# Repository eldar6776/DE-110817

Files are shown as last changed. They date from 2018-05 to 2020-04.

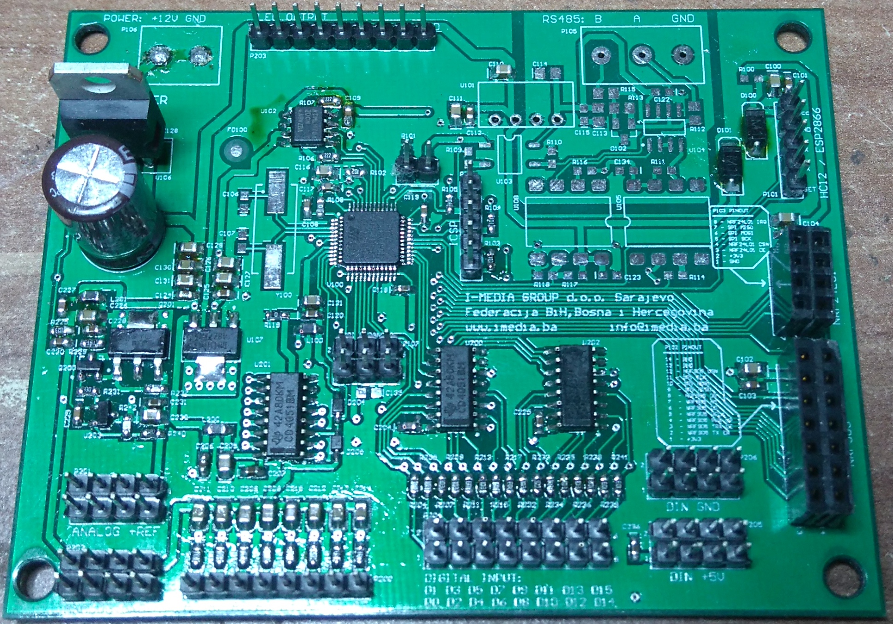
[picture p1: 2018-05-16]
RadioTxImg2.JPG

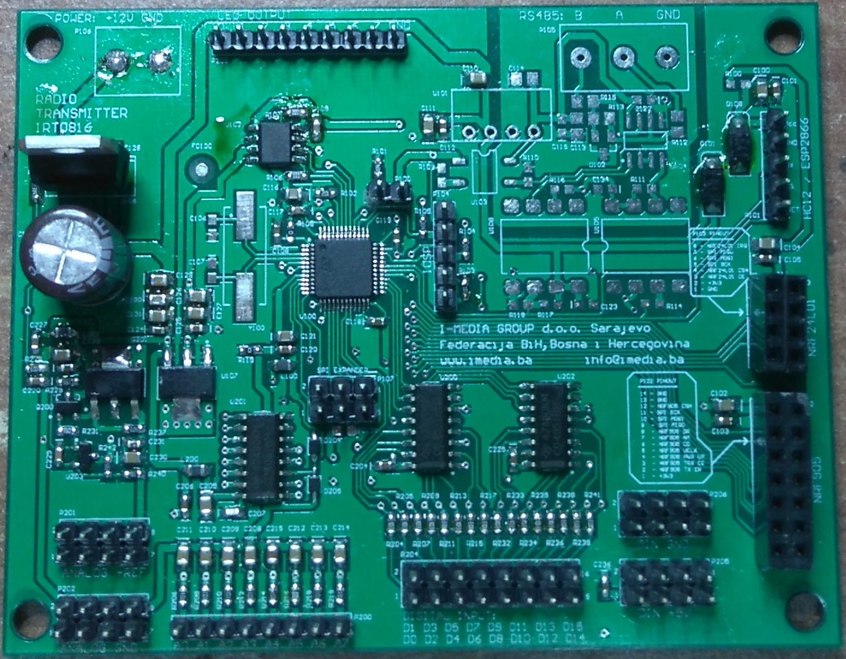
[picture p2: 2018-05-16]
RadioTxImg1.JPG

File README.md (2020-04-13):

# DE-110817
Two-Way Radio Link Transmitter Modul

this is a transmitter for DE-130817 receiver, with a secure radio link to control the concrete pumps. 8 digital inputs are transmitted from the receiver to the transmitter, the PWM driver temperature of 65 degrees Celsius sends a warning to the transmitter, 80 degrees Celsius switches off and blocks the PWM and relay outputs except the oil pump and bypass valve controls. the supply voltage is also monitored. The 433MHz HC-12 radio modules are more than enough range for a stable radio link. if the transmitter does not confirm the transmitter packet longer than 500ms, the receiver switches off the outputs and an LED signal is activated on the transmitter.

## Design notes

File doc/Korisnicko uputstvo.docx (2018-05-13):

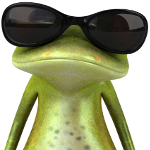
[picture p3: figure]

i MEDIA

__________________________________________________________________________________

Sistem radio kontrole pumpe za beton

Korisničko uputstvo

IRT0816 - Radio predajnik

8 analognih ulaza,

16 digitalnih ulaza,

8 led izlaza.

IRC0816 - Radio prijemnik

8 digitalnih ulaza,

16 relejnih izlaza,

16 PWM izlaza.

Posebne osobine:

- Podesiv indikator napona za većinu baterija ili akumulatora za napajanje predajnika: Nikal-Kadmium, suhi olovni akumulator, Litium-Ion, jednokratne alkalne baterije.
- Predupozorenje prazne baterije ispod 10% kapaciteta.
- Isključenje uređaja kod donjeg nivoa baterije što je ujedno i zaštita akumulatora od dubokog pražnjenja i oštećenja.
- Dvosmjerna radio komunikacija sa sigurnosnom funkcijom isključenja izlaza prijemnika kod prekida komunikacije >500 ms.
- Status prijemnika LED signalima na predajniku + stanje 8 digitalnih ulaza prijemnika koji se mogu koristiti za signalizaciju događaja sa prijemnika npr. min. nivou ulja, pregrijavanju, proradi zaštitnih uređaja, aktiviranju krajnjih ili sigurnosnih prekidača i sl.
- Stabilan izvor pozitivnog napona +3,3Vdc za referentni napon potenciometara spojenih na analogne ulaze.
- Zaštita PWM drivera od pregrijavanja sa signalom predupozorenja.
- RS485 interfejs za žičnu, backup, komunikaciju do 1km sa UTP, FTP, STP kablom za slučaj kvara ili smetnji radio komunikacije.

Fleksibilnost ugradnje:

- Jednostavno uspostavljanje optimalnog radio linka odabirom između 5 različitih radio modula i radnih frekvencija 315MHz, 433MHz, 868MHz, 915MHz, 2,4GHz, plug-and-play izmjenom bez dodatnih podešavanja za sigurnu radio kontrolu.
- Jednostavno podešavanje analognih ulaza za signale sa joystick potenciometara sa nulom na sredini klizača ili za signal potenciometara sa nulom signala na početku klizača
- Podesiva frekvencija PWM drivera za najoptimalniju kontrolu radnog uređaja sa što manjim gubicima i disipacijom temperature izlaznog PWM stepena.
- Mogućnost proširenja analognih/ digitalnih ulaza predajnika kao i pwm/relejnih izlaza prijemnika.
- Mogućnost ugradnje WiFi modula i kontrole prijemnika internet servisima tako da se modul može kristiti u Smart Home sistemu za on/off kontrolu 16~32 potrošača. PWM driver se bez ikakve preinake može koristiti za dimmer kontrolu 5~10 RGB ili 16~32 White LED nizova velike snage. Sa malim izmjenama, t.j. zamjenom tri komponente po kanalu, PWM driver se može transformisat u 16~32 kanalni DAC kojim se generišu kontrolni signali 0~10Vdc, a koji su industrijski standard i ulazni kontrolni signal kod mnogih LED dimmera

Karakteristike periferija:

- Signal na digitalnom ulazu prijemnika ili predajnika < 1Vdc je stanje logičke nule.
- Signal na digitalnom ulazu prijemnika ili predajnika > 2Vdc je stanje logičke jedinice.
- Maximalan pozitivni napon digitalnih ulaza prijemnika ili predajnika je < 30Vdc.
- Maksimalan pozitivni napon analognih ulaza predajnika je < 3,6Vdc.
- Signal na ulazu PWM drivera > 4Vdc postavlja izlaz PWM-a na visoki nivo (napon napajanja PWM drivera).
- Signal na ulazu PWM drivera < 3,5 Vdc postavlja izlaz PWM-a na niski nivo (GND PWM drivera).
- Izlaz PWM-a je N-MOSFET, zbog manjih gubitaka, u high-side switch spoju, t.j. kontrola pozitivnog napona. Upotrebljeni tip je maksimalnog radnog napona 100Vdc i 20A konstantne struje pri temperaturi kućišta do 100°C.
- Za temperature hladnjaka PWM drivera > 65°C aktivira se signal upozorenja na prijemniku.
- Temperatura hladnjaka PWM drivera > 80°C aktivira signal preopterećenja na prijemniku i aktivira zaštitnu funkciju koja isključuje sve izlaze prijemnika i onemogućava aktiviranje dok temperatura hladnjaka ne opadne ispod 65°C.
- Temperaturni senzor temperature hladnjaka PWM-a je NTC otpornik otpora 10K na temperaturi 25°C, na temperaturi 65°C je 2 K, a na temperaturi 80°C je 1,25 K.
- Na svim analognim ulazima su ugrađeni niskopropusni RC filteri ~150Hz koji eliminišu ili uveliko umanjuju smetnje nastale pomjeranjem klizača potenciometara koji su pred kraj radnog vijeka ili su već istrošeni.

Sadržaj uputstva:

1.0 Podešavanje i upotreba modula predajnika ................................... 6
2.0 Podešavanje i upotreba modula prijemnika.................................... 12
3.0 Pregled modula PWM drivera............................................................... 14
4.0 Električne sheme ......................................................................................... 17
5.0 Održavanje uređaja ................................................................................... 19
1. Podešavanje i upotreba modula predajnika :

raspored i namjena konektora na modulu radio predajnika

Kontrolni

taster

Konektor za

signalne LED

Konektor za

RS485 bus

Konektor za

napajanje

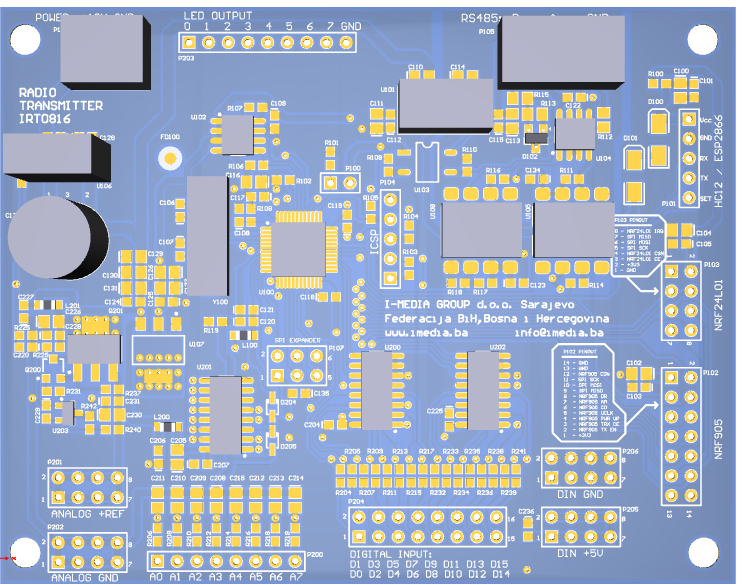
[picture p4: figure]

Konektor za modul proširenja

Konektor za

HC12 radio

modul i WiFi

Konektor za

NRF24L01

radio modul

Konektor za

NRF905 radio

modul

Masa za potenciometre

+3,3Vdc za

potenciometre

Analogni ulazi za potenciometre

Digitalni

ulazi

Masa za digitalne ulaze

+5Vdc za

digitalne ulaze

tabela napona standardnih ćelija

Tip ćelije/ napon | Olovna | Ni-Cd | Ni-MH | Li-ion
Napon ćelije (nominal.) | 2V | 1,2V | 1,2V | 3,7V
Napon pune ćelije | 2,40V | 1,45V | 1,41V | 4,20V
Napon prazne ćelije | 1,75V | 1,00V | 1,00V | 3,20~3,40V

  1.1 Način aktiviranja i izlaz iz funkcije podešavanja

Funkcija za podešavanje modula se aktivira tako da se pritisne kontrolni taster,

a zatim dok je taster pritisnut priključi napajanje predajnika. Sve statusne LED kratkim signalom označavaju da je funkcija aktivna. Nakon što je definisan parametar koji se podešava potrebno je kratko pritisnut kontrolni taster čime se nova vrijednost memoriše u eeprom i odmah je validna. Statusne LED sa tri kratka signala označavaju izlaz iz funkcije za podešavanje.

  1.2 Definisanje analognih ulaza

Kada je digitalni ulaz D0 spojen na +5Vdc i svi ostali digitalni ulazi su slobodni ili spojeni na masu, aktivirana funkcija podešavanja se odnosi na definisanje tipa signala na analognim ulazima. Analogne ulaze na koje će u toku rada uređaja biti spojen signal sa joystick potenciometra treba spojiti na 3,3Vdc, a analogne ulaze koji na koje će biti spojen signal sa standardnog potenciometra treba spojiti na masu. Nakon izlaza iz funkcije podešavanja definisani su analogni ulazi. Veoma je bitno da se ima u vidu da će sve promjene prvom konekcijom biti podešene i na prijemniku. Analogni ulaz predajnika na koji je spojen signal potenciometra joystick-a, na strani prijemnika kontroliše dva PWM izlaza koji su uvijek susjedni, a signal standardnog potenciometra kontroliše jedan PWM. Kada se promjeni definicija analognih ulaza treba i na strani prijemnika utvrditi novi raspored PWM izlaza.

  1.3 Podešavanje napona prazne baterije

Kada je digitalni ulaz D1 predajnika spojen na +5Vdc i svi ostali digitalni ulazi su slobodni ili spojeni na masu, aktivirana funkcija podešavanja se odnosi na definisanje napona prazne baterije. Napon napajanja treba podesiti na napon prazne baterij, a što se može izračunati prema „tabeli napona standardnih ćelija“, tako da se pomnoži broj članaka u bateriji za napajanja sa naponom prazne ćelije za korišteni tip. Najbolje je za napajanje koristiti podesivi izvor istosmjernog napona, a može se koristiti i ispražnjena baterij. Kada je napon definisan, kratko pritisnut kontrolni taster čime je izmjerena vrijednost memorisana kao donji prag napona baterije.

  1.4 Podešavanje napona pune baterije

Kada je digitalni ulaz D2 predajnika spojen na +5Vdc i svi ostali digitalni ulazi su slobodni ili spojeni na masu, aktivirana funkcija se odnosi na podešavanje napona pune baterije. Napon napajanja treba prije podesiti na napon pune baterije, a što se može izračunati prema „tabeli napona standardnih ćelija“, tako da se pomnoži broj članaka u bateriji za napajanja sa naponom pune ćelije za korišteni tip. Najbolje je za napajanje koristiti podesivi izvor istosmjernog napona, a može se koristiti i puna baterija. Kada je napon definisan, potrebno je kratko pritisnut kontrolni taster čime je izmjerena vrijednost memorisana kao napon pune baterije.

  1.5 Podešavanje frekvencije PWM izlaza 0 ~ 15

Kada je digitalni ulaz D3 predajnika spojen na +5Vdc i svi ostali digitalni ulazi su slobodni ili spojeni na masu, aktivirana je funkcija podešavanja frekvencije PWM signala za izlaze od 0 ~ 15. Signalom od 0 do 3,3Vdc na analognom ulazu A0 predajnika se podešava frekvencija PWM izlaza na prijemniku u rasponu od 24Hz do1526Hz. LED signali predstavljaju podešenu vrijednost i to za svaki LED koji svijetli konstantno frkvencija se uvećava za 200Hz, a trepćući signal označava uvećanje za 100Hz. Podešena frekvencija će biti podešena na prijemniku kod prve radio komunikacije sa predajnikom.

  1.6 Podešavanje frekvencije PWM izlaza 16 ~ 31

Kada je digitalni ulaz D4 predajnika spojen na +5Vdc i svi ostali digitalni ulazi su slobodni ili spojeni na masu, aktivirana je funkcija podešavanja frekvencije PWM signala za izlaze od 16 ~ 31. Signalom od 0 do 3,3Vdc na analognom ulazu A0 predajnika se podešava frekvencija PWM izlaza na prijemniku u rasponu od 24Hz do1526Hz. LED signali predstavljaju podešenu vrijednost i to za svaki LED koji svijetli konstantno frkvencija se uvećava za 200Hz, a trepćući signal označava uvećanje za 100Hz. Podešena frekvencija će biti podešena na prijemniku kod prve radio komunikacije sa predajnikom.

  1.7 Provjera statusa baterije

Kratkim pritiskom na kontrolni taster modula predajnika provjerava se status baterije prema LED signalima u rasponu od LED 0 za najmanji nivo do LED 7 za punu bateriju. Nakon 5 sekundi LED signali ponovo označavaju status prijemnika.

  1.8 Provjera statusa radio linka

Kratkim pritiskom na kontrolni taster modula predajnika za vrijeme provjere statusa baterije aktivira se provjera kvaliteta radio linka prema LED signalima u rasponu od LED 0 do LED 7. Ovaj mod ostaje aktivan do novog ciklusa napajanja

ili sledećeg pritiska na kontrolni taster nakon čega se ponovo LED signalima označava status prijemnika. Mjerenjem kvaliteta radio linka se mogu na vrijeme uočiti zone lošeg radio signala i izbjeći zastoji u radu mašine.

  1.9 Nuliranje analognih ulaza

Dužim pritiskom > 3s kontrolnog tastera modula predajnika, kada nije aktivna ni jedna druga funkcija podešavanja ili provjere, te otpuštanjem kontrolnog tastera, signali na analognim ulazima se definišu kao nulte pozicije potenciometara. Prije poziva ove funkcije potrebno je sve potenciometre dovesti u početne ili neutralne pozicije. Za potenciometre joystick-a napon signala u neutralnom položaju je idealno 1,65Vdc, a za ostale potenciometre je napon signala u početnoj poziciji 0Vdc, mada se ovom funkcijom mogu definisati nulte pozicije potenciometara i u bilo kojem drugom položaju npr. kada je signal sa potrošenog potenciometra nestabilan (šušti) na početku hoda, može se nula pomjeriti na dio klizača odakle je signal stabilan. Sve vrijednosti ispod nulte pozicije klizača su jednake nuli signala na izlazu PWM-a.

  1.10 RS485 interfejs za serijsku - backup konekciju

Komunikaciju između predajnika i prijemnika je moguće ostvariti povezivanjem RS485 interfejsa predajnika i prijemnika uvrnutom paricom dužine do 1000 m. Brzina serijske komunikacije je 9600 bps, a format 8-N-1. Ovim interfejsom se korištenjem seta komandi mogu podesiti svi parametri prijemnika i predajnika. Potreban je serijski teminal softver (npr. realterm) i konverter USB/RS485.

  1.11 HC-12 Radio modul

Radna frekvencija je u opsegu 433 – 473MHz podjeljena na 100 kanala. Uz izlaznu snagu od max. 100mW (20dB) i brzinu prenosa do 5000 bps na otvorenom prostoru moguće je ostvariti dvosmjernu komunikaciju do 1000 m. Ako je par ovih radio modula priključen na konektore P3 prijemnika i P101 predajnika, u toku inicijalizacije softvera prvi su odabir za radio link.

  1.12 NRF24L01+PA+LNA Radio modul

Radna frekvencija je 2,4GHz. Izlazna snaga predajnika je >100mW (>20dB), brzina prenosa do 2MB. Na otvorenom prostoru moguće je ostvariti dvosmjernu komunikaciju preko 700 m, brzine prijenosa 1MB. Ako je par ovih radio modula priključen na konektore P5 prijemnika i P103 predajnika, u toku inicijalizacije softvera drugi su odabir za radio link.

  1.13 NRF905 Radio modul

Radne frekvencije su u tri banda 433/868/915MHz. Izlazna snaga predajnika je 10mW (10dB) , brzina prenosa do 50 kbps. Na otvorenom prostoru moguće je ostvariti dvosmjernu komunikaciju do 300 m. Ako je par ovih radio modula priključen na konektore P4 prijemnika i P102 predajnika, u toku inicijalizacije softvera treći su odabir za radio link uspostavljen na bandu 433MHz.

  1.14 LED signalizacija stanja digitalnih ulaza prijemnika i greške

Konektor P203 modula predajnika omogućava monitoring raznih statusa prijemnika i predajnika sa 8 LED dioda koje se spajaju anodama na pinove 1 do 8 konektora P203, a sve katode se spajaju na zajednički pin 9. Serijski otpornici su ugrađeni na modulu i nije ih potrebno dodavati eksterno. Struja izlaza za LED diode sa padom napona od 2V je ~3mA, a za LED diode sa padom napona 3V je ~1mA, što treba uzeti u obzir kada se uređaj napaja baterijama.

Stanje aktivnog digitalnog ulaza na prijemniku se signalizira konstantno svjetlećom LED na predajniku sa istim brojem (LED 0 za digitalni ulaz DIN 0) i obratno, LED je neaktivna kada je digitalni ulaz neaktivan.

Signalizacija greške se označava sa tri kratke promjene stanja LED signala i pauzom od tri sekunde. To znači ako LED svijetli zato što je taj digitalni ulaz aktivan, onda će emitovanje svjetla biti tri puta kratko prekinuto i nakon svake tri sekunde ponovo, a ako je LED bila neaktivna onda će tri puta kratko zasvjetliti i nakon tri sekunde pauze ponavljati ovaj signal.

Značenje signaliziranih grešaka:

LED 0 - napon baterije za napajanje predajnika ispod 10% - upozorenje

LED 1 - baterija za napajanje predajnika prazna - isključenje

LED 2 - greška modula I2C PWM kontrolera - isključenje

LED 3 - temperatura hladnjaka PWM izlaza veća od 65°C - upozorenje

LED 4 - temperatura hladnjaka PWM izlaza veća od 80°C - isključenje

LED 5 - greška NTC temistora za mjerenje temperature PWM - isključenje

LED 6 - prekid radio linka > 500 ms - isključenje

LED 7 - prekid u napajanju prijemnika - isključenje

  1.15 Spajanje analognih ulaza

Svi analogni ulazi su za napone od 0 do 3,3Vdc (!!! NE 5Vdc), za što je na PCB-u modula preajnika obezbjeđen stabilan referentni izvor napona na konektoru P201. Potenciometri na ulazu se spajaju na konektore P200, P201 i P202.

ANALOG +REF (P201)

A0; A1....A7 (P200)

ANALOG GND (P202)

  1.16 Spajanje digitalnih ulaza

Svi digitalni ulazi su predviđeni za ulazni napon do 30Vdc. Na PCB-u modula predajnika se nalaze konektori P204; P205; P206 za dva načina spajanje digitalnih ulaza: sa eksternim izvorom i internim izvorom. Kod spajanja sa internim izvorom, na konektoru P205 je obezbjeđen izvor +5Vdc za beznaponski kontakt koji se drugim izvodom spaja na digitalne ulaze na konektoru P204. Ako se koristi eksterni izvor, minus pol izvora se spaja na DIN GND konektor P206 modula, a pozitivan pol izvora se spaja na digitalne ulaze na konektoru P204. Stanje digitalnog ulaza u odnosu na napon izvora je opisano u dijelu „Karakteristike periferija“.

spajanje digitalnog ulaza za internim izvorom

DIN +5V(P205) D0; D1.....D15 (P204)

spajanje digitalnog ulaza za eksternim izvorom

0~30V D0; D1.....D15 (P204)

GND DIN GND(P206)

  1.17 Spajanje kontrolnog tastera

Za korištenje funkcija: „provjera statusa baterije, provjera statusa radio linka, nuliranje analognih ulaza “, kao i za podešavanja modula predajnika potreban je spoj kontrolnog tastera. Ovaj taster bi trebao biti zaštićen od slučajnog pritiska u toku rada sa predajnikom zbog mogućnosti neželjenog aktiviranja funkcije „nuliranje analognih ulaza“ , a samim tim i zastoja u radu dok se ova funcija ponovo provede.

spajanje kontrolnog tastera

P100/1 P100/2

2. Podešavanje i upotreba modula prijemnika :

raspored i namjena konektora na modulu radio predajnika

LOOP VENTIL

RELEJ 15

RELEJ 9

RELEJ 10

RELEJ 11

RELEJ 12

RELEJ 13

RELEJ 13

RELEJ 14

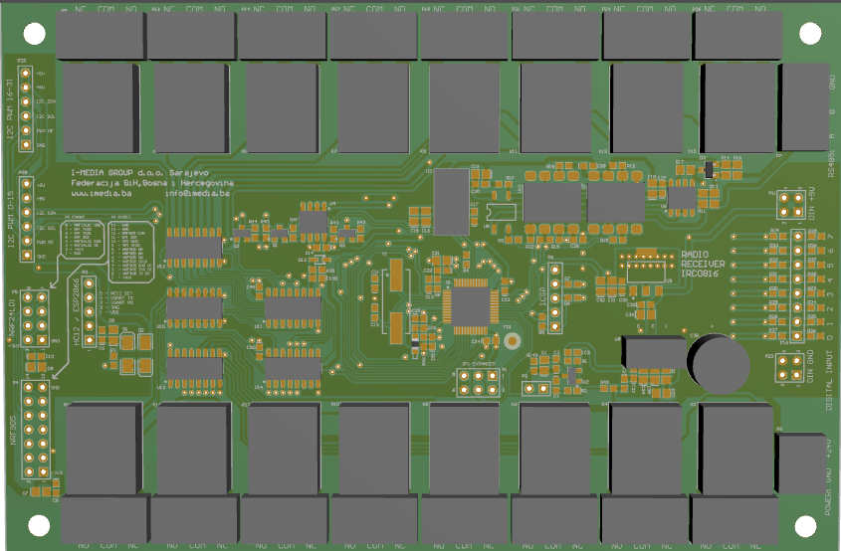
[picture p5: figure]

Konektor NTC senzora

Masa za digitalne ulaze

Konektor za

napajanje

RELEJ 7

RELEJ 6

RELEJ 5

RELEJ 8

RELEJ 4

RELEJ 3

RELEJ 2

RELEJ 1

Konektor za

NRF905

radio modul

Konektor za

PWM kontroler 2

modul

Konektor za

RS485 bus

Digitalni

ulazi

+5Vdc za

digitalne ulaze

Konektor za

NRF24L01

radio modul

Konektor za

PWM kontroler 1

modul

Konektor za

HC12 radio

modul i WiFi

  2.1 NTC senzor temperature hladnjaka PWM izlaza

Tip NTC senzora je pisan u dijelu „Karakteristike periferija“ i korišten je veoma dostupan i najčešće korišteni tip 10K na 25°C. Kada se koristi potrebno je tijelo NTC termistora sa malo termoprovodne paste učvrstiti na hladnjak PWM izlaza i dvožičnim provodnikom spojiti na P2 modula prijemnika. Ovaj provodnik je potrebno odvojiti od provodnika PWM i relejnih izlaza koji su izvor smetnji.

Monitoring teperature hladnjaka PWM drajvera se može isključiti postavljanjem jumpera (kratak spoj) na konektor P2 u slučaju npr. neispravnog NTC termistora ili kada se ne koristi PWM driver.

  2.2 Spajanje digitalnih ulaza

Svi digitalni ulazi su predviđeni za ulazni napon do 30Vdc. Na PCB-u modula prijemnika se nalaze konektori P11; P16; P23 za dva načina spajanje digitalnih ulaza: sa eksternim izvorom i internim izvorom. Kod spajanja sa internim izvorom, na konektoru P11 je obezbjeđen izvor +5Vdc za beznaponski kontakt koji se drugim izvodom spaja na digitalne ulaze na konektoru P16. Ako se koristi eksterni izvor, minus pol izvora se spaja na DIN GND konektor P23 modula, a pozitivan pol izvora se spaja na digitalne ulaze na konektoru P16. Stanje digitalnog ulaza u odnosu na napon izvora je opisano u dijelu „Karakteristike periferija“.

spajanje digitalnog ulaza za internim izvorom

DIN +5V(P11) D0; D1.....D7 (P16)

spajanje digitalnog ulaza za eksternim izvorom

0~30V D0; D1.....D7 (P16)

GND DIN GND(P23)

  2.3 Spajanje PWM kontrolera

Na modul prijemnika je moguće priključiti dva 16 kanalna PWM kontrolera za generisanje PWM signala 0-5Vdc. Kada se koristi drugi PWM kontroler, na prijemniku je potrebno ugraditi modul proširenja analognih ulaza. Rad modula prijemnika je moguć sa i bez modula PWM kontrolera. Ako je modul PWM kontrolera priključen na PCB prijemnika, nakon priključenja napona, softver će registrovati modul i u slučaju kvara ili isključenja u toku rada prijavit će grešku modula te isključiti sve izlaze prijemnika. Ako modul PWM kontrolera nije bio priključen kod uključenja napajanja prijemnika, PWM funkcija izlaza se ne koristi te prijemnik služi kao on/off rejeni kontroler.

Pregled modula PWM drivera :

PCB i raspored komponenti PWM Drivera IPD1624

PWM

izlaz 5

PWM

izlaz 4

PWM

izlaz 3

PWM

izlaz 2

PWM

izlaz 1

PWM

izlaz 0

PWM

izlaz 7

PWM

izlaz 6

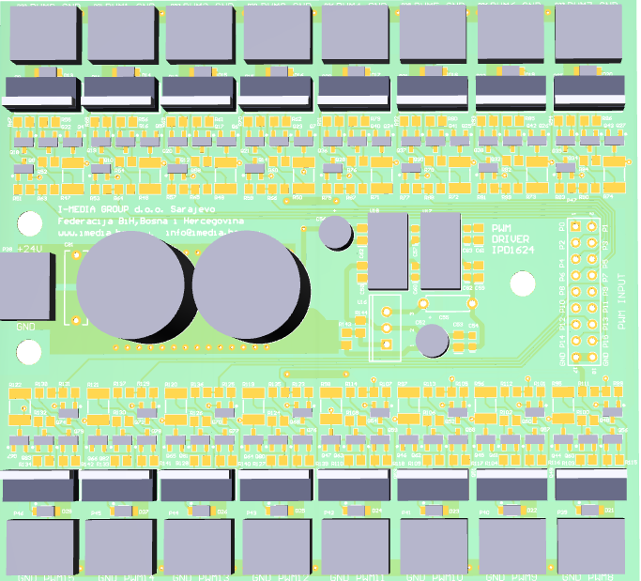
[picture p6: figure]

PWM

izlaz 9

PWM

izlaz 10

PWM

izlaz 11

PWM

izlaz 12

PWM

izlaz 13

PWM

izlaz 14

PWM

izlaz 15

Napajanje

PWM

drivera

PWM

ulazi

0 ~ 15

PWM

izlaz 8

PWM driver IPD1624 je predviđen kao univerzalan PWM izlazni stepen za širok opseg opterećenja i radnih napona, te kao takav nema implementiranu prekostrujnu zaštitu i koju je potrebno izvesti eksterno prema opterećenju koje se spaja na izlaz. Zaštita se može izvesti serijskom vezom staklenog rastalnog osigurača (tromog T ili brzog F) i priključenog opterećenja t.j. radnog uređaja (proporcionalni elektro ventil, servo pozicioner, aktuator), a što treba provjeriti u specifikaciji za taj uređaj. Primjer spoja zaštite je skiciran ispod.

SF52 (5A, 100V)

ventil

T2A

PWM GND

izlaz osigurač

Niti na jedan od PWM izlaza drivera se ne smije priključivati izvor napajanja bilo da je PWM driver priključen na napajanje ili da je napajanje isključeno. Ovo bi za posljedicu imalo pregorijevanje gate otpornika izlaznog MOSFET-a, zaštitne zener diode ili pnp gate-driver tranzistora.

Ukoliko je potreban bilo kakav paralelan rad PWM drivera i nekog drugog kontrolnog sklopa, potrebno je ili napraviti preklopnik ručna komanda – radio komada ili na izlaz PWM-a koji je u paralelnom spoju sa dodatnom kontrolom ugraditi diodu za blokadu pozitivnog napona sa izlaza prema unutrašnjem sklopu PWM drivera. Dioda treba biti dimenzionisana prema struji priključenog opterećenja. Treba voditi računa da je pad napona na diodi oko 0,5 V što uz veću struju opterećenja od npr. 2A daje disipaciju od 1W, tako da je potrebno pobrinuti se za odvođenje viška toplote sa diode na hladnjak .

spoj za preklopnik ručna komanda – radio komada

SF52 (5A, 100V)

PWM

T2A

izlaz

ventil

GND

Ručna

komanda

relej

Odabir

kontrole

spoj za blokadu pozitivnog napona sa ručne kontrole prema PWM driveru

MBRF20100CT SF52 (5A, 100V)

ventil

T2A

PWM

izlaz

GND

Ručna

komanda

Na sva induktivna opterećenja kontrolisana PWM driverom koja nemaju ugrađen snubber, obavezno je ugraditi flyback diodu bar duplo veće struje od struje kontrolisanog induktiviteta i bar duplo većeg reversnog napona od napona napajanja PWM drivera. Bez eliminisanja smetnji koje nastaju kod isključenja napajanja induktivitetu, moguća su spontana, nekontrolisana uključenja izlaza PWM drivera kao i nekontrolisani reseti mikrokontrolera.

spoj flyback - zaštitne diode na induktivno opterećenje (elektroventil 2A, 24Vdc)

SF52 (5A, 100V)

T3,15A

ventil

PWM GND

izlaz

Električne sheme :

spajanje modula PWM kontrolera, PWM izlaza i radio modula prijemnika

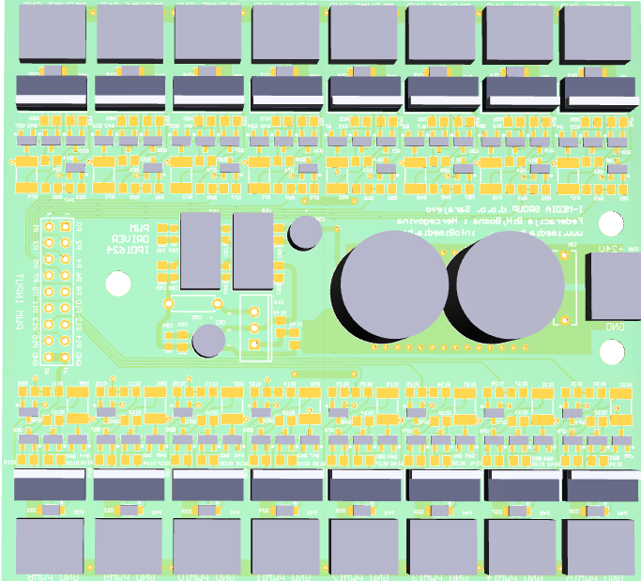
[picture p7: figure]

HC12

radio modul

vcc

PWM kontroler

!!! Kod povezivanja modula obrati pažnju na crveni marker kabla.

spajanje radio modula predajnika

HC12

radio modul

vcc

!!! Kod povezivanja modula obrati pažnju na crveni marker kabla.

Održavanje uređaja:

Ukoliko je signal sa potenciometra do te mjere nestabilan da prolazi kroz RC filter analognih ulaza, može se (za prvu pomoć) između signala sa klizača potenciometra i mase spojiti kondenzator 10 ~47 uF/10V pazeći da se negativni pol kondenzatora spoji na masu, a pozitivni na klizač. Veći kapacitet kondenzatora ima za rezultat veću stabilnost signala ali ujedno i sporiji odziv na promjene položaja potenciometra. Naročito je važno kašnjenje do nule signala t.j. kada se klizač brzo pomjeri u nultu poziciju, signal će kasniti i još neko vrijeme ostati aktivan dok ne postigne nultu vrijednost, pa je najbolje potenciometre koji uzrokuju smetnje zamjeniti novim.

BETTON PLANET © 2007–2018 I-Media Group d.o.o SarajevoPage 15

IRT0816 – Radio transmiter & IRC0816 – Radio receiver

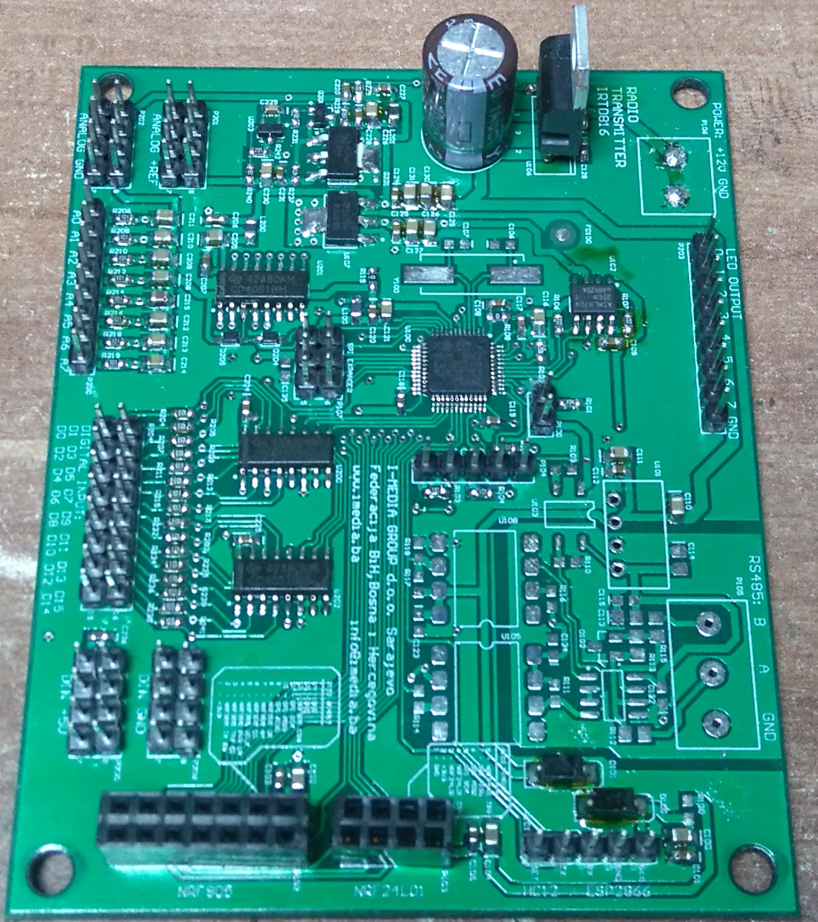
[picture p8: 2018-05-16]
RadioTxImg3.JPG

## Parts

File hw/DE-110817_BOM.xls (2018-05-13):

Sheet: BOM Report
Bill of Materials |  |  | CuC & Com
Source Data From: |  | DE-110817.PrjPcb
Project: |  | DE-110817.PrjPcb
Variant: |  | None
Creation Date: | 13.5.2018. | 03:15:46
Print Date: | 43233 | 43233.13601
Footprint | Comment | LibRef | Designator | Description | Quantity
0805 | 10uF | C0805 | C100, C102, C104, C110, C111, C113, C114, C116, C126, C127, C129, C130, C131, C205, C208, C209, C210, C211, C212, C213, C214, C215, C226, C230 | Ceramic Chip Capacitor - Standard | 24
0603 | 100nF | C0603 | C101, C103, C105, C108, C109, C112, C115, C117, C118, C119, C121, C122, C123, C124, C125, C128, C132, C134, C135, C200, C201, C202, C203, C204, C206, C207, C216, C217, C218, C219, C220, C221, C222, C223, C224, C225, C227, C228, C231, C232, C233, C234, C23 | Ceramic Chip Capacitor - Standard | 44
0603 | 22pF | C0603 | C106, C107 | Ceramic Chip Capacitor - Standard | 2
0603 | 1uF | C0603 | C120 | Ceramic Chip Capacitor - Standard | 1
CAPPR5-10x16 | 1000uF | EKA00DD410D00 | C133 | Aluminum Electrolytic Capacitor, Radial Style with Long Leads: 1000uF, 16V | 1
0603 | 10nF | C0603 | C229 | Ceramic Chip Capacitor - Standard | 1
SMA | 1N4001 | 10MQ060N | D100, D101 | Schottky Rectifier | 2
SOT23_3L | SM712 | 824022 | D102 | TVS Diode WE-TVS-Standard, VRWM=5.0V | 1
ONSC-SOD-323-2-477-02_V | 3V3 | MM3Z33VT1G | D200, D201, D202, D203, D206, D207, D208, D209, D210, D211, D212, D213, D214, D215, D216, D217 | Zener Voltage Regulator, 300 mW, 2-Pin SOD-323, Pb-Free, Tape and Reel | 16
SOD323 | 1N4148 | BAS321 | D204, D205 | General-purpose Diode | 2
SMD-0805 | 120R | 74279202 | L100, L200, L201 | SMD EMI Suppression Ferrite Bead WE-CBF, Z = 120 Ohm | 3
HDR1X2 | CONFIG | Header 2 | P100 | Header, 2-Pin | 1
HDR1X5 | HC12_RADIO | Header 5 | P101 | Header, 5-Pin | 1
HDR2X7 | nRF905 | Header 7X2 | P102 | Header, 7-Pin, Dual row | 1
HDR2X4 | NRF24L01 | Header 4X2 | P103 | Header, 4-Pin, Dual row | 1
HDR1X5 | ULINK_ICSP | Header 5 | P104 | Header, 5-Pin | 1
TERMINAL BLOK 3 | TERMINAL BLOK 3 | TERMINAL BLOK 3 | P105 | 3 pinski terminal blok konektor | 1
TERMINAL BLOK 2 | TERMINAL BLOK 2 | TERMINAL BLOK 2 | P106 | 2 pinski terminal blok | 1
HDR2X3 | SPI_EXPANDER | Header 3X2 | P107 | Header, 3-Pin, Dual row | 1
HDR1X8 | ANALOG_INPUT | Header 8 | P200 | Header, 8-Pin | 1
HDR2X4 | ANIN_VREF | Header 4X2 | P201 | Header, 4-Pin, Dual row | 1
HDR2X4 | ANIN_VSS | Header 4X2 | P202 | Header, 4-Pin, Dual row | 1
HDR1X9 | LED | Header 9 | P203 | Header, 9-Pin | 1
HDR2X8 | DIGITAL_INPUT | Header 8X2 | P204 | Header, 8-Pin, Dual row | 1
HDR2X4 | DIN_VDD | Header 4X2 | P205 | Header, 4-Pin, Dual row | 1
HDR2X4 | DIN_VSS | Header 4X2 | P206 | Header, 4-Pin, Dual row | 1
318-08 | MMBT2222 | MMBT2222ALT1 | Q200 | General Purpose Transistor NPN Silicon | 1
SOT223_N | BCP56 | BCP56 | Q201 | NPN Medium Power Transistor | 1
ERA-0603 | NF | ERAV | R100 | Metal Film Thermosensitive Chip Resistor, 0.56 Ohm to 10k Ohm Range, 5% Tolerance, 0603 Size, 0.063 W | 1
ERA-0603 | 100K | ERA3Y | R101 | Rectangular Thick Film Chip Resistor, 10 Ohm to 330k Ohm Range, 0.1% and 0.5% Tolerance, 0603 Size, 0.063 W | 1
ERA-0603 | 10K | ERA3Y, ERA3Y, ERAV, ERAV, ERAV, ERAV, ERAV, ERAV, ERAV, ERAV, ERAV, ERAV, ERAV, ERAV, ERAV, ERAV, ERAV, ERAV, ERAV, ERAV, ERAV, ERAV, ERAV, ERAV, ERAV, ERAV, ERAV, ERAV, ERAV, ERAV, ERAV, ERAV, ERAV, ERAV | R102, R103, R200, R201, R202, R203, R204, R205, R207, R209, R211, R213, R215, R217, R220, R221, R222, R223, R226, R227, R228, R230, R232, R233, R234, R235, R236, R238, R239, R241, R243, R244, R245, R246 | Rectangular Thick Film Chip Resistor, 10 Ohm to 330k Ohm Range, 0.1% and 0.5% Tolerance, 0603 Size, 0.063 W, Rectangular Thick Film Chip Resistor, 10 Ohm to 330k Ohm Range, 0.1% and 0.5% Tolerance, 0603 Size, 0.063 W, Metal Film Thermosensitive Chip Resis | 34
ERA-0603 | 100R | ERA3Y, ERA3Y, ERAV, ERAV, ERAV, ERAV, ERAV, ERAV, ERAV, ERAV | R104, R105, R206, R208, R210, R212, R214, R216, R218, R219 | Rectangular Thick Film Chip Resistor, 10 Ohm to 330k Ohm Range, 0.1% and 0.5% Tolerance, 0603 Size, 0.063 W, Rectangular Thick Film Chip Resistor, 10 Ohm to 330k Ohm Range, 0.1% and 0.5% Tolerance, 0603 Size, 0.063 W, Metal Film Thermosensitive Chip Resis | 10
ERA-0603 | 2K2 | ERA3Y | R106, R107 | Rectangular Thick Film Chip Resistor, 10 Ohm to 330k Ohm Range, 0.1% and 0.5% Tolerance, 0603 Size, 0.063 W | 2
ERA-0603 | 0R | ERA3Y, ERAV | R108, R119 | Rectangular Thick Film Chip Resistor, 10 Ohm to 330k Ohm Range, 0.1% and 0.5% Tolerance, 0603 Size, 0.063 W, Metal Film Thermosensitive Chip Resistor, 0.56 Ohm to 10k Ohm Range, 5% Tolerance, 0603 Size, 0.063 W | 2
ERA-0603 | 330R | ERAV, ERA3Y, ERAV, ERAV, ERAV, ERAV, ERAV, ERAV, ERAV | R109, R114, R116, R247, R248, R251, R252, R253, R254 | Metal Film Thermosensitive Chip Resistor, 0.56 Ohm to 10k Ohm Range, 5% Tolerance, 0603 Size, 0.063 W, Rectangular Thick Film Chip Resistor, 10 Ohm to 330k Ohm Range, 0.1% and 0.5% Tolerance, 0603 Size, 0.063 W, Metal Film Thermosensitive Chip Resistor, 0 | 9
ERA-0603 | 470R | ERAV | R110, R111 | Metal Film Thermosensitive Chip Resistor, 0.56 Ohm to 10k Ohm Range, 5% Tolerance, 0603 Size, 0.063 W | 2
ERA-0805 | 10R | ERA6Y | R112, R115 | Rectangular Thick Film Chip Resistor, 10 Ohm to 1M Ohm Range, 0.1% and 0.5% Tolerance, 0805 Size, 0.1 W | 2
ERA-0805 | 120R | ERA6Y | R113 | Rectangular Thick Film Chip Resistor, 10 Ohm to 1M Ohm Range, 0.1% and 0.5% Tolerance, 0805 Size, 0.1 W | 1
ERA-0603 | 510R | ERAV | R117 | Metal Film Thermosensitive Chip Resistor, 0.56 Ohm to 10k Ohm Range, 5% Tolerance, 0603 Size, 0.063 W | 1
ERA-0603 | 1K | ERAV | R118 | Metal Film Thermosensitive Chip Resistor, 0.56 Ohm to 10k Ohm Range, 5% Tolerance, 0603 Size, 0.063 W | 1
ERA-0603 | 330K | ERAV | R224 | Metal Film Thermosensitive Chip Resistor, 0.56 Ohm to 10k Ohm Range, 5% Tolerance, 0603 Size, 0.063 W | 1
ERA-0603 | 82K | ERAV | R225 | Metal Film Thermosensitive Chip Resistor, 0.56 Ohm to 10k Ohm Range, 5% Tolerance, 0603 Size, 0.063 W | 1
ERA-0603 | 560R | ERAV | R229 | Metal Film Thermosensitive Chip Resistor, 0.56 Ohm to 10k Ohm Range, 5% Tolerance, 0603 Size, 0.063 W | 1
ERA-0603 | 33R | ERAV | R231 | Metal Film Thermosensitive Chip Resistor, 0.56 Ohm to 10k Ohm Range, 5% Tolerance, 0603 Size, 0.063 W | 1
ERA-0603 | 4K7 | ERAV | R237 | Metal Film Thermosensitive Chip Resistor, 0.56 Ohm to 10k Ohm Range, 5% Tolerance, 0603 Size, 0.063 W | 1
ERA-0603 | 1K8 | ERAV | R240 | Metal Film Thermosensitive Chip Resistor, 0.56 Ohm to 10k Ohm Range, 5% Tolerance, 0603 Size, 0.063 W | 1
ERA-0603 | 5K6 | ERAV | R242 | Metal Film Thermosensitive Chip Resistor, 0.56 Ohm to 10k Ohm Range, 5% Tolerance, 0603 Size, 0.063 W | 1
ERA-0603 | 220R | ERAV | R249, R250 | Metal Film Thermosensitive Chip Resistor, 0.56 Ohm to 10k Ohm Range, 5% Tolerance, 0603 Size, 0.063 W | 2
STM-LQFP48_N | STM32F103C8T6 | STM32F103C8T6 | U100 | ARM Cortex-M3 32-bit MCU, 64 KB Flash, 20 KB Internal RAM, 37 I/Os, 48-pin LQFP, -40 to 85 degC, Tray | 1
B0505S-1W | B0505S/D-1W | B0505S/D | U101 | 1W isolated dc dc converter | 1
SOIC-SN8_N | AT24C1024 | 24AA64/SN | U102 | 64Kbit, 400kHz, 1.7V, I2C Serial EEPROM, 8-Pin SOIC 150mil, Commercial Temperature | 1
SOP4 | PS2501L | PC817 optocoupler | U103 | 4-Pin Phototransistor Optocoupler | 1
D008_L | SN75176BD | SN75176BD | U104 | Differential Bus Transceiver | 1
SMD-8 | 6N137 | 6N137 | U105, U108 | High CMR, High Speed TTL Compatibile Optocoupler | 2
TO220ABN | L7805CV | L7805CV | U106 | Positive Voltage Regulator | 1
ZZ311 | REG1117-3.3 | REG1117-3.3 | U107 | 800mA and 1A Low Dropout Positive Regulator 2.85V, 3.3V, 5V, and Adjustable | 1
M16A_N | HCF4051M013TR | CD4051BCM | U200, U201, U202 | 8-Channel Analog Multiplexer/Demultiplexer | 3
SOT23-3_N | TL431CL3T | TL431CL3T | U203 | Programmable Voltage Reference, 2.5 to 36V, 3-Pin SOT23-3, Tape and Reel | 1
HC49/4H_SMX | 8MHz | HC49/4H_SMX | Y100 | Surface Mount Quartz Crystal | 1
 |  |  |  |  | 203
Approved |  | Notes

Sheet: Project Information
Project Full Path | F:\SkyDrive\OtvoreniProjekti\SuperBeton\hw\hw\DE-110817.PrjPcb
Project Filename | DE-110817.PrjPcb
Variant Name | None
Data-Source Filename | DE-110817.PrjPcb
Data-Source Full Path | F:\SkyDrive\OtvoreniProjekti\SuperBeton\hw\hw\DE-110817.PrjPcb
Title | CuC & Com
Total Quantity | 203
Report Time | 03:15:46
Report Date | 13.5.2018.
Report Date & Tine | 13.5.2018. 03:15:46
Output Name | Bill of Materials
Output Type | BOM_PartType
Output Generator Name | BOM
Output Generator Description | Bill of Materials

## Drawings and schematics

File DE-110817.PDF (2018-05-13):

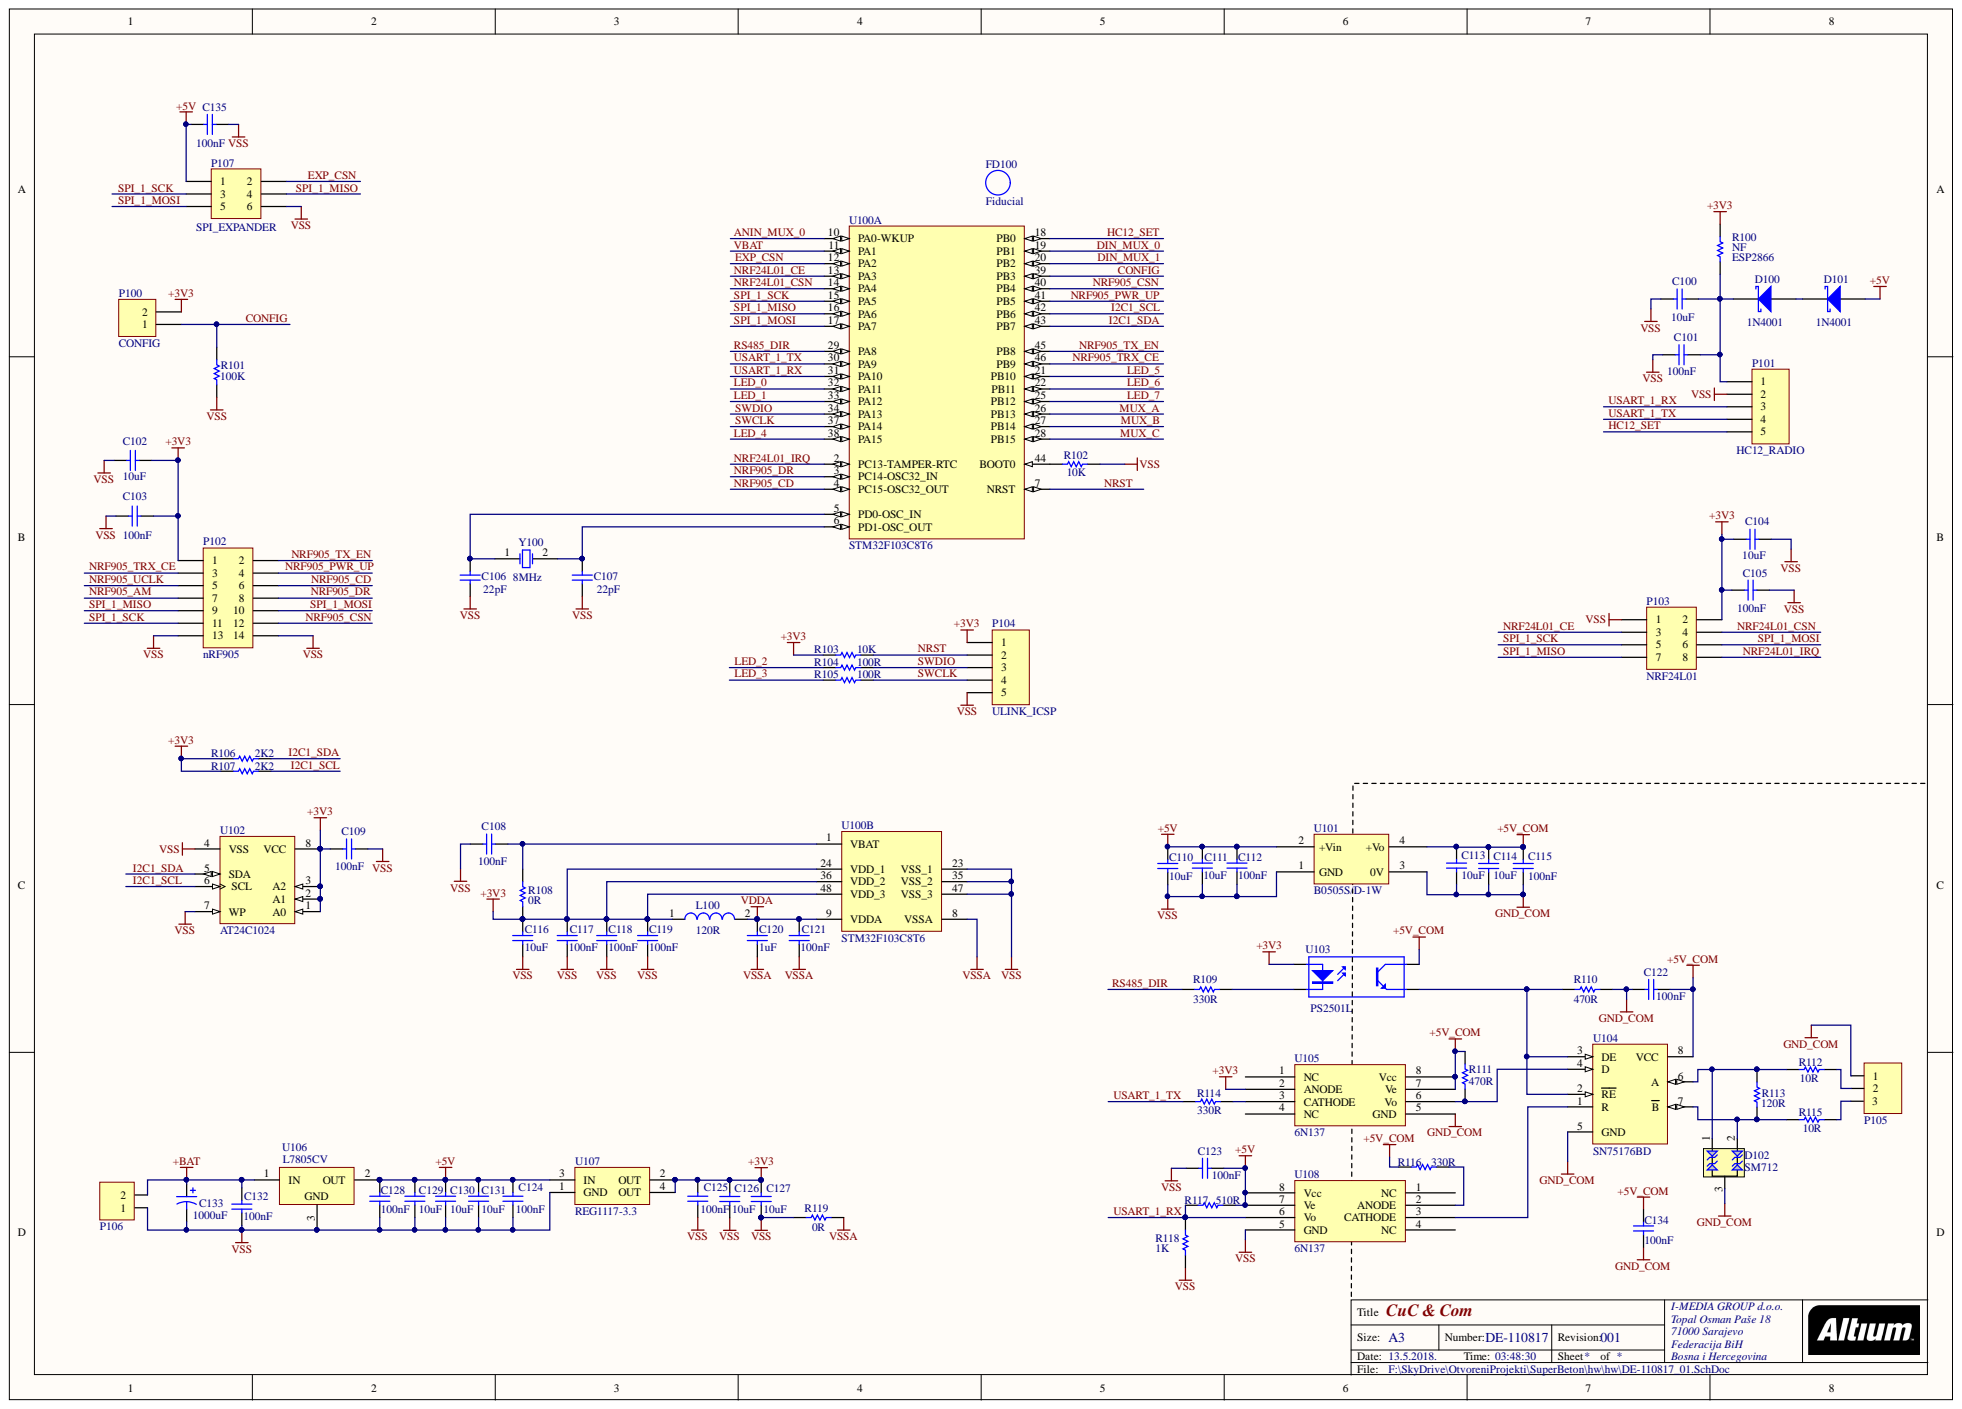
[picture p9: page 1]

CuC & Com Title | I-MEDIA GROUP d.o.o. Topal Osman Paše 18 71000 Sarajevo Federacija BiH Bosna i Hercegovina

Size: A3 | Number: DE-110817 | Revision: 001
Date: 13.5.2018. Time: 03:48:30 | | Sheet * of *

F:\SkyDrive\OtvoreniProjekti\SuperBeton\hw\hw\DE-110817_01.SchDoc

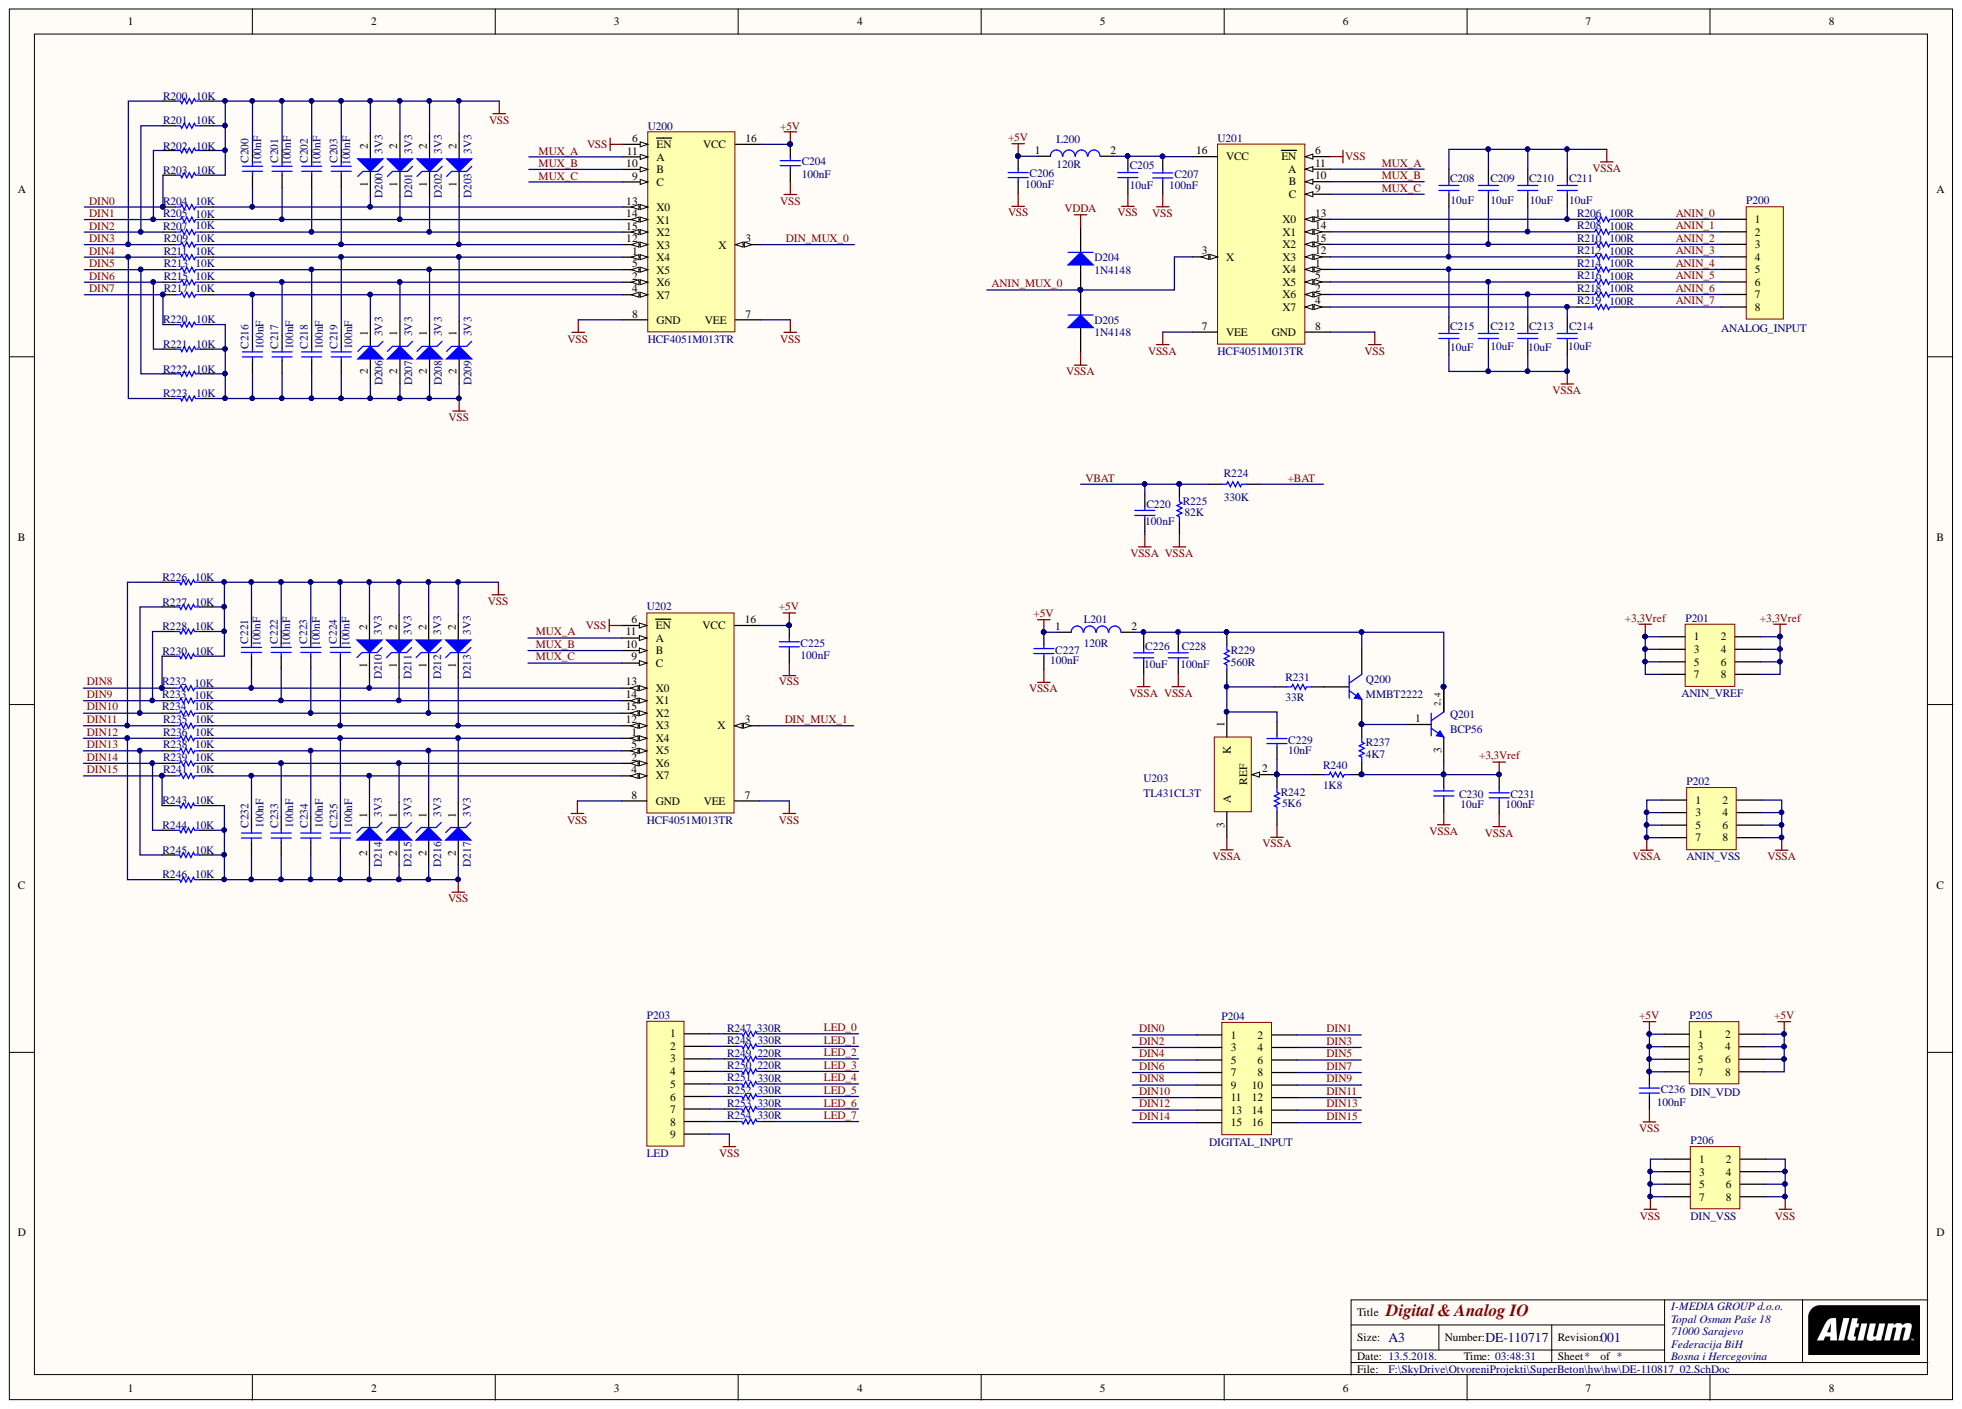
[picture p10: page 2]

Digital & Analog IO Title | I-MEDIA GROUP d.o.o. Topal Osman Paše 18 71000 Sarajevo Federacija BiH Bosna i Hercegovina

Size: A3 | Number: DE-110717 | Revision: 001
Date: 13.5.2018. Time: 03:48:31 | | Sheet * of *

F:\SkyDrive\OtvoreniProjekti\SuperBeton\hw\hw\DE-110817_02.SchDoc

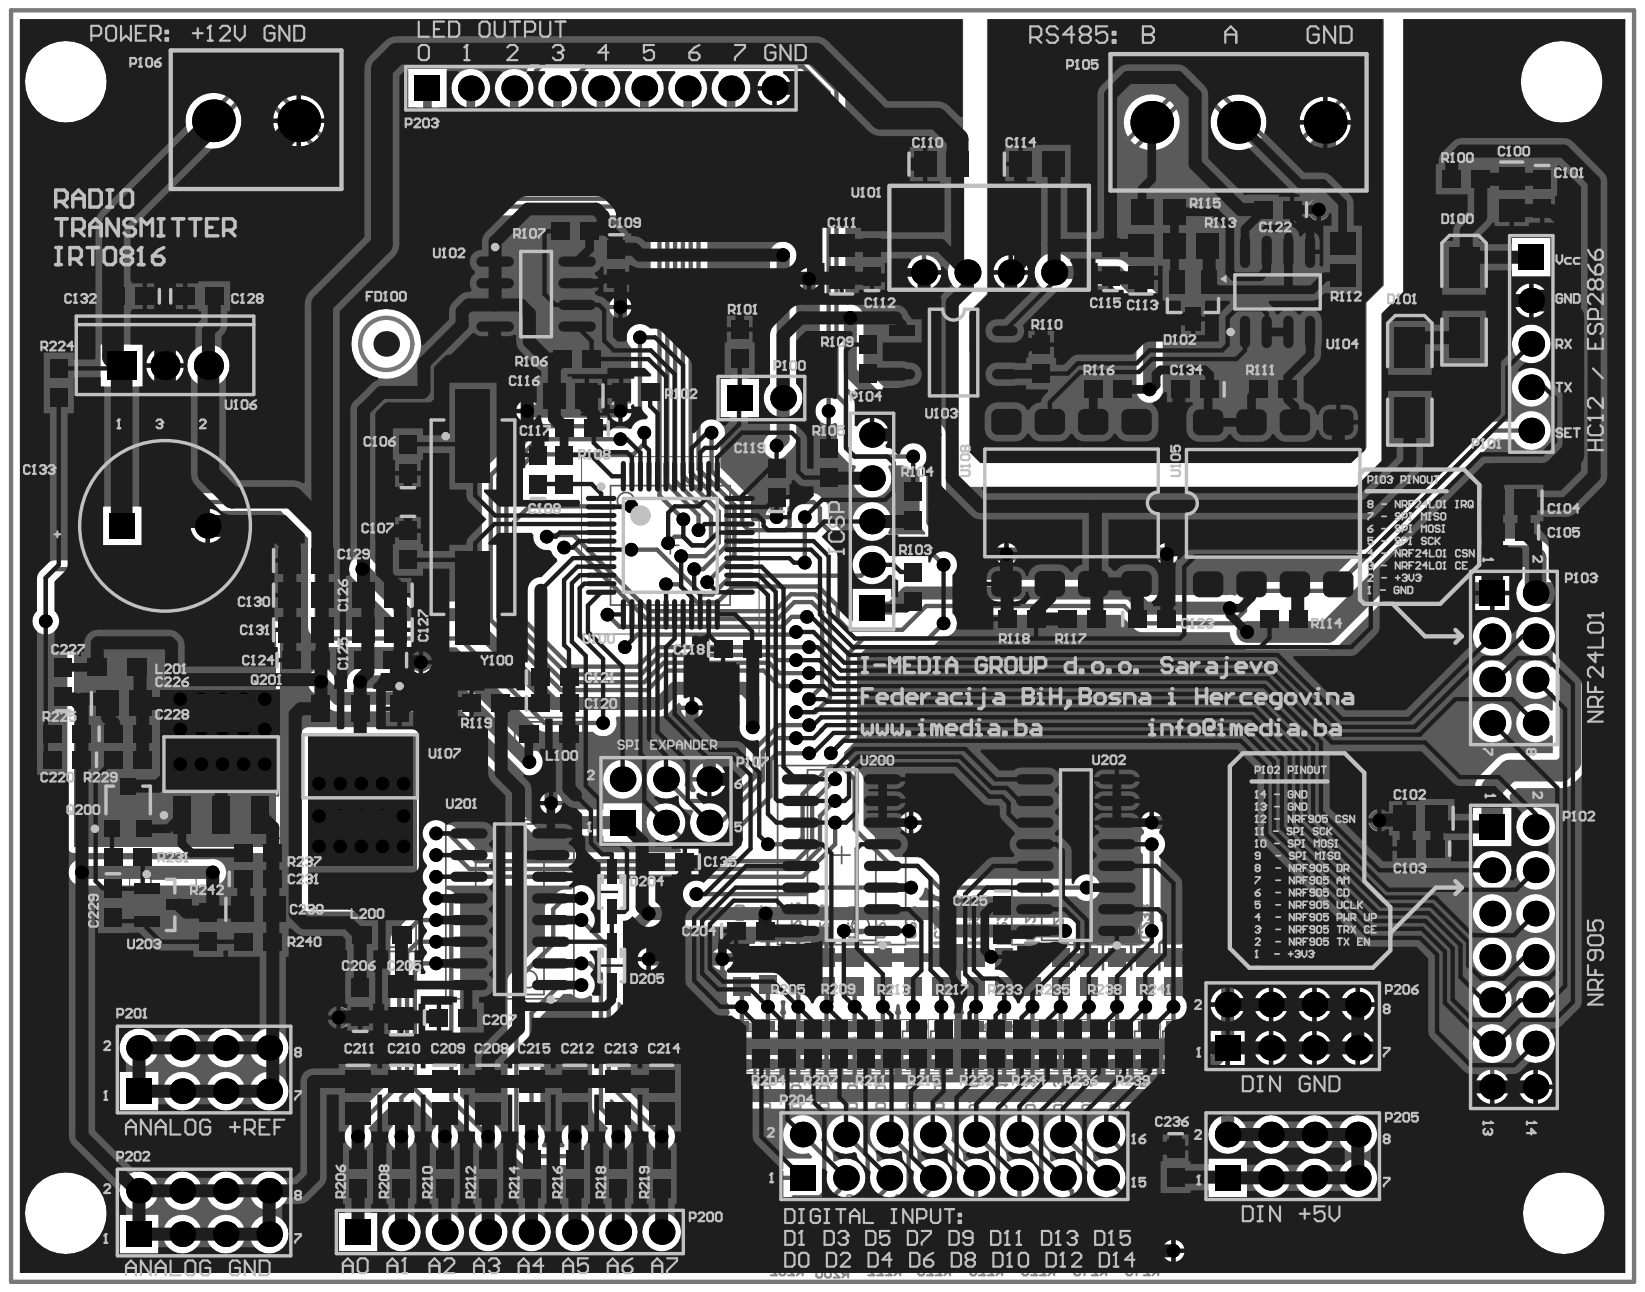
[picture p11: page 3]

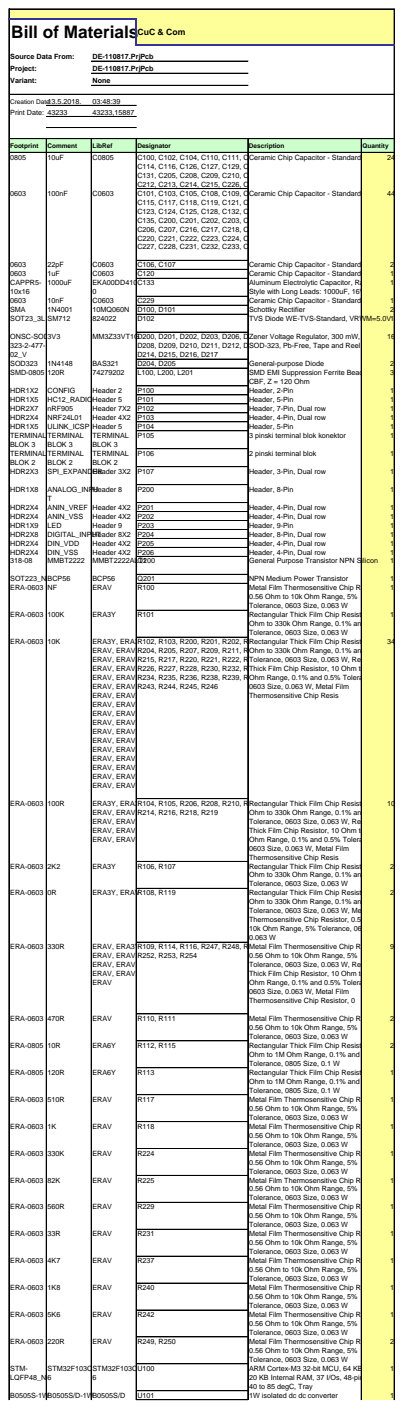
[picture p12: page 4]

Bill of MaterialsCuC & Com

Footprint | Comment | LibRef | Designator | Description | Quantity

Style with Long Leads: 1000uF, 16V

Zener Voltage Regulator, 300 mW, 2-Pin
SOD-323, Pb-Free, Tape and Reel

0.56 Ohm to 10k Ohm Range, 5%
Tolerance, 0603 Size, 0.063 W

Ohm to 330k Ohm Range, 0.1% and 0.5%
Rectangular Thick Film Chip Resistor, 10
Tolerance, 0603 Size, 0.063 W, Rectangular
Thick Film Chip Resistor, 10 Ohm to 330k
Ohm Range, 0.1% and 0.5% Tolerance,
0603 Size, 0.063 W, Metal Film
Thermosensitive Chip Resis

Tolerance, 0603 Size, 0.063 W, Metal Film
Thermosensitive Chip Resistor, 0.56 Ohm to
10k Ohm Range, 5% Tolerance, 0603 Size,
Metal Film Thermosensitive Chip Resistor,
Thermosensitive Chip Resistor, 0

Ohm to 1M Ohm Range, 0.1% and 0.5%
Tolerance, 0805 Size, 0.1 W

20 KB Internal RAM, 37 I/Os, 48-pin LQFP, -
40 to 85 degC, Tray

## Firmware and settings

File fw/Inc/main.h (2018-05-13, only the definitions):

#define EE_BUFFER_SIZE				16			// reserved RAM buffer for eeprom related operation
#define EE_TIMEOUT     				20			// 20 ms eeprom operation timeout
#define EE_BLOCK_SIZE				256			// max. byte number in one block for single write operation
#define EE_READ  					0xaf		// command to read page 0 from i2c eeprom
#define EE_READ_PAGE_1  			0xa7		// command to read page 1 from i2c eeprom
#define EE_WRITE 					0xae		// command to write page 0 in i2c eeprom
#define EE_WRITE_PAGE_1 			0xa6		// command to write page 1 in i2c eeprom
#define EE_PAGE_SIZE				0x10000		// 64 kByte eeprom page size
#define EE_PAGE_COUNT				512			// number of pages
#define EE_WRITE_DELAY				10			// 10 ms delay to complete write operation
#define EE_TRIALS					100			// number of i2c operation trials
#define EE_ANIN0_TYPE_ADDRESS					0x00
#define EE_ANIN1_TYPE_ADDRESS					0x01
#define EE_ANIN2_TYPE_ADDRESS					0x02
#define EE_ANIN3_TYPE_ADDRESS					0x03
#define EE_ANIN4_TYPE_ADDRESS					0x04
#define EE_ANIN5_TYPE_ADDRESS					0x05
#define EE_ANIN6_TYPE_ADDRESS					0x06
#define EE_ANIN7_TYPE_ADDRESS					0x07
#define EE_ANIN0_NULL_OFFSET_ADDRESS			0x10
#define EE_ANIN1_NULL_OFFSET_ADDRESS			0x12
#define EE_ANIN2_NULL_OFFSET_ADDRESS			0x14
#define EE_ANIN3_NULL_OFFSET_ADDRESS			0x16
#define EE_ANIN4_NULL_OFFSET_ADDRESS			0x18
#define EE_ANIN5_NULL_OFFSET_ADDRESS			0x1a
#define EE_ANIN6_NULL_OFFSET_ADDRESS			0x1c
#define EE_ANIN7_NULL_OFFSET_ADDRESS			0x1e
#define EE_BATTERY_TYPE_ADDRESS					0x20
#define EE_EMPTY_BATTERY_VOLTAGE_ADDRESS		0x21
#define EE_WARNING_BATTERY_VOLTAGE_ADDRESS		0x23
#define EE_FULL_BATTERY_VOLTAGE_ADDRESS			0x25
#define EE_NTC_WARNING_TEMPERATURE_ADDRESS		0x30
#define EE_NTC_SHUTDOWN_TEMPERATURE_ADDRESS		0x32
#define EE_SUPPLY_SHUTDOWN_VOLTAGE_ADDRESS		0x34
#define EE_PWM_0_15_FREQUENCY_ADDRESS			0x40
#define EE_PWM_16_31_FREQUENCY_ADDRESS			0x42
#define EE_RS485_INTERFACE_ADDRESS				0x50
#define EE_RS485_GROUP_ADDRESS					0x52
#define EE_RS485_BROADCAST_ADDRESS				0x54
#define EE_RS485_BAUDRATE_ADDRESS				0x56
#define EE_HC12_BAUDRATE_ADDRESS				0x60
#define EE_HC12_CHANEL_ADDRESS					0x61
#define EE_HC12_LINK_TIMEOUT_ADDRESS			0x62
#define EE_NRF24L01_BAUDRATE_ADDRESS			0x70
#define EE_NRF24L01_CHANEL_ADDRESS				0x71
#define EE_NRF24L01_LINK_TIMEOUT_ADDRESS		0x72
#define EE_NRF905_BAUDRATE_ADDRESS				0x80
#define EE_NRF905_BAND_ADDRESS					0x81
#define EE_NRF905_CHANEL_ADDRESS				0x82
#define EE_NRF905_LINK_TIMEOUT_ADDRESS			0x83

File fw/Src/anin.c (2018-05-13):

/**
 ******************************************************************************
 * File Name          : anin.c
 * Date               : 04/01/2018 5:19:19
 * Description        : analog input processing
 ******************************************************************************
 *
 *
 ******************************************************************************
 */
 
 
/* Includes ------------------------------------------------------------------*/
#include "anin.h"
#include "dio.h"
#include "common.h"
#include "main.h"


/* Typedef -------------------------------------------------------------------*/
/* Define --------------------------------------------------------------------*/
/* Variable ------------------------------------------------------------------*/
extern ADC_HandleTypeDef hadc1;

volatile uint32_t anin_timer;
uint16_t anin0;
uint8_t	 anin0_type;
uint8_t	 anin0_set_type;
uint16_t anin0_null;
uint16_t anin1;
uint8_t	 anin1_type;
uint8_t	 anin1_set_type;
uint16_t anin1_null;
uint16_t anin2;
uint8_t	 anin2_type;
uint8_t	 anin2_set_type;
int16_t  anin2_null;
uint16_t anin3;
uint8_t	 anin3_type;
uint8_t	 anin3_set_type;
uint16_t anin3_null;
uint16_t anin4;
uint8_t	 anin4_type;
uint8_t	 anin4_set_type;
uint16_t anin4_null;
uint16_t anin5;
uint8_t	 anin5_type;
uint8_t	 anin5_set_type;
uint16_t anin5_null;
uint16_t anin6;
uint8_t	 anin6_type;
uint8_t	 anin6_set_type;
uint16_t anin6_null;
uint16_t anin7;
uint8_t	 anin7_type;
uint8_t	 anin7_set_type;
uint16_t anin7_null;
uint8_t batt_type;
uint16_t vbatt;
uint16_t vbatt_min;
uint16_t vbatt_warning;
uint16_t vbatt_max;
uint8_t pwm[PWM_BUFFER_SIZE];


/* Macro ---------------------------------------------------------------------*/
/* Program code   ------------------------------------------------------------*/
void ANIN_Service(void)
{
	static enum
	{
		ANIN_INIT				= 0x00,
		ANIN_MULTIPLEXER		= 0x01,
		ANIN_BATTERY_VOLTAGE	= 0x02
		
	} ANIN_ServiceState = ANIN_INIT;
	
	ADC_ChannelConfTypeDef sConfig;
	uint32_t pwm_cnt;

	switch(ANIN_ServiceState)
	{
		/** ==========================================================================*/
		/**     A N A L O G   C O N V E R T E R     I N I T I A L I Z A T I O N		  */
		/** ==========================================================================*/
		case ANIN_INIT:
		{	
			ClearBuffer(pwm, PWM_BUFFER_SIZE);
			ANIN_StartTimer(ANIN_POWERON_DELAY);			
			ANIN_ServiceState = ANIN_MULTIPLEXER;
			break;
		}		
		/** ==========================================================================*/
		/**   M U L T I P L E X E R	  A N A L O G   I N P U T   C O N V E R S I O N   */
		/** ==========================================================================*/		
		case ANIN_MULTIPLEXER:
		{
			sConfig.Channel = ADC_CHANNEL_0;
			sConfig.Rank = 1;
			sConfig.SamplingTime = ADC_SAMPLETIME_1CYCLE_5;
			if (HAL_ADC_ConfigChannel(&hadc1, &sConfig) != HAL_OK)
			{
				_Error_Handler(__FILE__, __LINE__);
			}
			
			ClearBuffer(pwm, PWM_BUFFER_SIZE);
			/**
			*	set adc chanel 0 input and start conversion
			*	of multiplexer analog input 0 value
			*/
			SelectMuxInput0();
			HAL_ADC_Start(&hadc1);
			HAL_ADC_PollForConversion(&hadc1, ADC_TIMEOUT);
			anin0 = HAL_ADC_GetValue(&hadc1);			
			
			if(anin0_type == 1)
			{
				/**
				*	for common type potentiometer check limits of measured analog signal value:
				*	for wiper position below preset null position round pwm value to zero
				*	and for wiper position close to maximum set pwm to 100%
				*/
				if(anin0 < anin0_null) pwm[0] = 0;
				else if((anin0 - anin0_null) > 4080) pwm[0] = 0xff;
				else pwm[0] = ((anin0 - anin0_null) / 16);
			}
			else if(anin0_type == 2)
			{
				/**
				*	for joystick type potentiometer pwm value increase twice for same 
				*	wiper deflection in common type potentiometer  
				*	if wiper position is close to maximum deflection 
				* 	in either direction set pwm to 100%
				*/
				if(anin0 > anin0_null)
				{
					if((anin0 - anin0_null) > 2040) pwm[0] = 255;
					else pwm[0] = ((anin0 - anin0_null) / 8);					
				}
				else if(anin0 < anin0_null)
				{
					if((anin0_null - anin0) > 2040) pwm[1] = 255;
					else pwm[1] = ((anin0_null - anin0) / 8);				
				}
			}		
			/**
			*	convert multiplexer analog input 1 value
			*/
			SelectMuxInput1();
			HAL_ADC_Start(&hadc1);
			HAL_ADC_PollForConversion(&hadc1, ADC_TIMEOUT);
			anin1 = HAL_ADC_GetValue(&hadc1);
			
			if(anin1_type == 1)
			{
				if(anin1 < anin1_null) pwm[anin0_type] = 0;
				else if((anin1 - anin1_null) > 4080) pwm[anin0_type] = 0xff;
				else pwm[anin0_type] = ((anin1 - anin1_null) / 16);
			}
			else if(anin1_type == 2)
			{
				if(anin1 > anin1_null)
				{
					if((anin1 - anin1_null) > 2040) pwm[anin0_type] = 255;
					else pwm[anin0_type] = ((anin1 - anin1_null) / 8);					
				}
				else if(anin1 < anin1_null)
				{
					if((anin1_null - anin1) > 2040) pwm[anin0_type + 1] = 255;
					else pwm[anin0_type + 1] = ((anin1_null - anin1) / 8);					
				}
			}
			/**
			*	convert multiplexer analog input 2 value
			*/
			SelectMuxInput2();
			HAL_ADC_Start(&hadc1);
			HAL_ADC_PollForConversion(&hadc1, ADC_TIMEOUT);
			anin2 = HAL_ADC_GetValue(&hadc1);
			pwm_cnt = anin0_type + anin1_type;
			
			if(anin2_type == 1)
			{
				if(anin2 < anin2_null) pwm[pwm_cnt] = 0;
				else if((anin2 - anin2_null) > 4080) pwm[pwm_cnt] = 0xff;
				else pwm[pwm_cnt] = ((anin2 - anin2_null) / 16);
			}
			else if(anin2_type == 2)
			{
				if(anin2 > anin2_null)
				{
					if((anin2 - anin2_null) > 2040) pwm[pwm_cnt] = 255;
					else pwm[pwm_cnt] = ((anin2 - anin2_null) / 8);
				}
				else if(anin2 < anin2_null)
				{
					if((anin2_null - anin2) > 2040) pwm[pwm_cnt + 1] = 255;
					else pwm[pwm_cnt + 1] = ((anin2_null - anin2) / 8);
				}
			}		
			/**
			*	convert multiplexer analog input 3 value
			*/
			SelectMuxInput3();
			HAL_ADC_Start(&hadc1);
			HAL_ADC_PollForConversion(&hadc1, ADC_TIMEOUT);
			anin3 = HAL_ADC_GetValue(&hadc1);
			pwm_cnt = anin0_type + anin1_type + anin2_type;
			
			if(anin3_type == 1)
			{
				if(anin3 < anin3_null) pwm[pwm_cnt] = 0;
				else if((anin3 - anin3_null) > 4080) pwm[pwm_cnt] = 0xff;
				else pwm[pwm_cnt] = ((anin3 - anin3_null) / 16);
			}
			else if(anin3_type == 2)
			{
				if(anin3 > anin3_null)
				{
					if((anin3 - anin3_null) > 2040) pwm[pwm_cnt] = 255;
					else pwm[pwm_cnt] = ((anin3 - anin3_null) / 8);
				}
				else if(anin3 < anin3_null)
				{
					if((anin3_null - anin3) > 2040) pwm[pwm_cnt + 1] = 255;
					else pwm[pwm_cnt + 1] = ((anin3_null - anin3)  / 8);
				}
			}		
			/**
			*	convert multiplexer analog input 4 value
			*/
			SelectMuxInput4();
			HAL_ADC_Start(&hadc1);
			HAL_ADC_PollForConversion(&hadc1, ADC_TIMEOUT);
			anin4 = HAL_ADC_GetValue(&hadc1);
			pwm_cnt = anin0_type + anin1_type + anin2_type + anin3_type;
			
			if(anin4_type == 1)
			{
				if(anin4 < anin4_null) pwm[pwm_cnt] = 0;
				else if((anin4 - anin4_null) > 4080) pwm[pwm_cnt] = 0xff;
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

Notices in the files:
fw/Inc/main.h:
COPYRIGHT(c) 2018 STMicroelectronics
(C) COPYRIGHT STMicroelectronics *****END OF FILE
